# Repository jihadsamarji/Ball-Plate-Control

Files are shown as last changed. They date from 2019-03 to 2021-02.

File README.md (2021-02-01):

-------------------------------------
The Project is Still under Construction
-------------------------------------
# Ball-Plate-Control
This is a project done for a Master Thesis in the Electromechanical Engineering (specialization: Mechatronics),
it is about the design and control of a Ball and Plate Didactic Device.
This device is intended to be developed into a Commercial device and maybe sold to educational institutes or young apprentices in the field of Control Systems. 

The Project is Explained entirely on : [Presentation Video](https://youtu.be/tS8yI4Vpe_U) 

## Getting Started

These instructions will get you a copy of the project up and running on your local machine for development and testing purposes. See deployment for notes on how to deploy the project on a live system.

### Prerequisites

things you need to install before running the code:
- Arduino IDE
- Python 3.7
- Python PiP
- Python IDE (Pycharm is recommended)

Run the following commands in your command terminal after installing "PIP"
```
pip install opencv-python==3.4.5.20
pip install Django
pip install Pillow
pip install image
pip install imutils
pip install numpy
pip install pyserial
pip install pytz
pip install setuptools
pip install sqlparse
pip install wheel
```

## Deployment

- Make sure you run the "solveequation.py" code first to generate the dictionary file. (found in /Software/Lookuptable/)
- Then place the dictionary file called "data.txt" in the same directory of the "interface.py" code. (found in /Software/Interface/)
- Connect an Arduino and upload the arduino code "Full_Program.ino" using the arduino IDE.
- Make sure you have a Camera attached on your system. (otherwise, you will get an opencv error when running)
- Run the code "interface.py" . (found in /Software/Interface/) 

## Simulation Files
The simulation files are found in ( /Software/Matlab & Simulation/)

## Contributing

Please Contact me on jmz_mmz@hotmail.com for any contribution requests.

## Versioning

Versioning was done using GIT

## Authors

* **Jihad Alsamarji** - *Masters in Electromechanical Engineering* - [JISA_leb](https://github.com/jihadsamarji)

See also the list of [contributors](https://github.com/jihadsamarji/Ball-Plate-Control/graphs/contributors) who participated in this project.

## License

This project is licensed under the MIT License - see the [LICENSE.md](LICENSE.md) file for details

## Acknowledgments

I would first like to thank my thesis advisors and supervisors of the SAAS department at Université Libre de Bruxelles; Micheal KINNAERT, Laurent CATOIRE,Christoph MERTENS.
The door to my supervisors was always open whenever I ran into problems or had a question about my research or writing.
They consistently allowed this paper to be my own work, but steered me in the right direction whenever I needed it.
I would also like to thank the members of my dissertation committee - not only for their time and extreme patience, but for their intellectual contributions to my development as an Engineer.
In Addition, I like to express my gratitude to the open source Community that helped a lot in overcoming software and computational challenges during the study.
I must express my very profound gratitude to my parents, friends and to my girlfriend for providing me with unfailing support and continuous encouragement throughout my study and through the process of researching and writing this thesis.
This accomplishment would not have been possible without them.
Thank you.

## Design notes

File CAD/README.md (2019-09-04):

# Computer Aided Design
Please Proceed to the "/Thesis/test Bench/" folder to find the CAD files used to build the prototype.
The Asset folder, contains some 3d models found on the internet.

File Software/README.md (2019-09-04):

## Software Content
The software section is divided into several folder:
- Arduino (Contains equipment testing and calibration files and the final Full Program that is going to be running on the arduino in parallel with the image processing thread on the computer)
- Interface (Contains the GUI source code)
- LookUptable (Contains the code that generates a lookup table text file that helps the GUI to map between angle Alpha and Beta) 
- Matlab & Simulation (Contains the State space modelling and simulation files + simscape numerical simulation + recorded experimental data)

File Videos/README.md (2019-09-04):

# Ball-Plate-Control
## Videos
The submitted videos gives a demo of the GUI when the project was undergoing testing.

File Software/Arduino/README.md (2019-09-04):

#Arduino Files
To run the plant with the GUI you will be only needing the "Full_Program.ino" files.
The rest of the codes are only to test partially some functionalities of the equipments used for the plant.
You can notice that there is a file for the touchscreen, however, this was discontinued due to the extreme sensor noise.

## Caution 
All of these files are calibrated for a certain sensor and actuator that the Author owns. 
You should modify the calibration part of the code when using your own hardware.

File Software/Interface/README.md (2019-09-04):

# Interface (GUI)
The "interface.py" file is the code that contains entirely the GUI code, However, you should make sure that the lookup table which is the text file called "data.txt" is present within this directory to ensure that the code runs.
Another thing you should check is that a functional camera is attached to your system otherwise you will get opencv errors.
Lastly, you have the option to plot and record readings in realtime while using the GUI which will be stored in the "log.txt" file. This log file can be used with matlab later on to compare graphs.

##Additional information
The "Gettime.py" is just a simple code to record time delays between the GUI and the Arduino. You might actually never use this code, so please ignore it if you find it useless.

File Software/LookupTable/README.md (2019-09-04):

# Lookup Table Generation
Due to the non linear relation between the angle Alpha and Theta, a lookup table can be generated to map between these to angles by running the "solveEquation.py".
The generated file "data.txt" needs to be placed in the interface directory afterwards if you intend it to be used by the GUI.

## Caution
The "solveEquation.py" is manually adjusted to cope with the non linearities of the Author's actuator. So make sure you read it and understand it well, and then modify it to work with your actuator.

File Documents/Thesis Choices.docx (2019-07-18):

# Models (2 choices):

## 2 perpendicular Motors (with a base pole in the center):

Simpler (one motor to control orientation X and one for Y) (+)

Requires less Equipment -> Cheaper (+)

## 3 Motors 360/3 (without a base pole in the center):

More complex (any combination of 3 angles will give a certain inclination) (-)

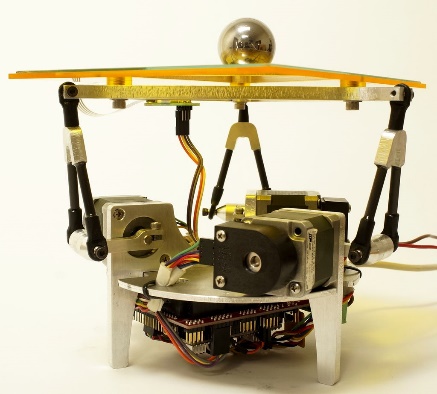
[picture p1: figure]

More Equipment -> More expensive (-)

Robust (+)

More of a Challenge (harder modelling and Control) (-)

# Requirements:

## Motors:

- Servo:

Easier to control (+)

Already comes with an encoder (+)

Much better for dynamic behavior (++)

Constant Torque to speed change (+)

Less power consumption (+)

- Stepper:

Harder to control (needs a drive) (-)

Needs an encoder for feedback (-)

Very accurate (++)

Higher power consumption (-)

## Position Sensor:

- Camera:

Requires a backend for image processing (--)

Can detect ball even if not on plate (predictive behavior) (++)

Adaptable for any kind of base shape (+)

Needs an Aditional Structure to hold the Camera (-)

- Resistive Touch screen:

Can only detect ball if ball Is on the base (no predictive behavior) (-)

Easy measurements (position X and Y) (++)

Limited to Base shape and Dimension (-)

No need for backend (++)

Noisy (---)

Requires a certain pressure to give readings (---)

## Control PCB:

- Arduino or Any Commercial Board:

Needs a Servo Shield module to power up the servos (-)

Commercially Available and Cheap (++)

Easy to Program and implement (+)

- Custom Made Board:

Needs time to Design and Build (--)

Needs Experience in Electronics and PCB design software (-)

Complicated and Hard to Program (-)

Customized for our Need → efficient and optimal (+)

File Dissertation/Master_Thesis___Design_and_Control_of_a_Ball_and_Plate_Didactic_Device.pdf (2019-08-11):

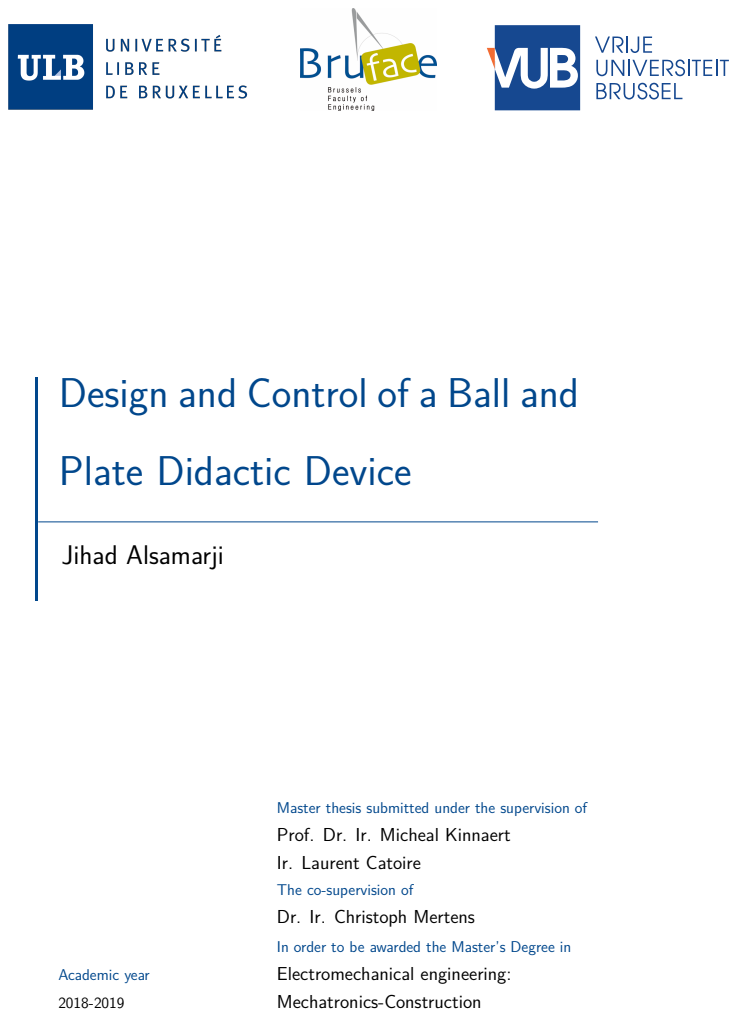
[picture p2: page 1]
Jihad Alsamarji; Academic year

Design and Control of a Ball and

Plate Didactic Device

Master thesis submitted under the supervision of
Prof. Dr. Ir. Micheal Kinnaert
Ir. Laurent Catoire

The co-supervision of
Dr. Ir. Christoph Mertens

In order to be awarded the Master’s Degree in
Electromechanical engineering:
Mechatronics-Construction

Abstract

This project tackles the design and control problem of a two DOF

ball and plate system to build a commercial didactic device that helps

young engineers to practice their control theory knowledge. Two sensing

techniques are proposed to measure the displacement of the ball; a resis-

tive touch screen or a camera with some image processing. The plant is

designed with CAD and operated using an arduino. A computer is also

connected to the plant for image processing using a GUI developed with

python. The plant is modelled and simulated using Matlab and Simulink.

Multiple PD controllers are compared and validated on the real system.

Keywords: 2DOF Ball and Plate System, Didactic Device, Mechanical Design,

Image Processing GUI, Control Design.

## Acknowledgement

I would first like to thank my thesis advisors and supervisors of the SAAS depart-

ment at Université Libre de Bruxelles; Micheal KINNAERT, Laurent CATOIRE,

Christoph MERTENS.

The door to my supervisors was always open whenever I ran into problems or had

a question about my research or writing. They consistently allowed this paper to

be my own work, but steered me in the right direction whenever I needed it.

I would also like to thank the members of my dissertation committee - not only

for their time and extreme patience, but for their intellectual contributions to my

development as an Engineer.

In Addition, I like to express my gratitude to the open source Community that

helped a lot in overcoming software and computational challenges during the

study.

I must express my very profound gratitude to my parents, friends and to my

girlfriend for providing me with unfailing support and continuous encouragement

throughout my study and through the process of researching and writing this

thesis. This accomplishment would not have been possible without them.

Thank you.

## List of Figures

1 | A demonstration of different Ball-Plate plants. From left to right:
2DOF, 3DOF and 6DOF | | 3
2 | A sketch of the 2DOF Ball-Plate prototype done prior to the
design stage | | 5
3 | Mechanical design dimensions (mm) | 11
4 | Mechanical design features | 12
5 | Electrical wiring of the touch screen sensor | 13
6 | Touch screen inner circuit taken from [7] | 14
7 | Pin states for reading each coordinate | 15
8 | Electrical wiring of the camera sensor | 15
9 | simple flowchart of touch screen code on arduino | 17
10 | Two programs running in parallel | 18
11 | Graphical user interface developped with the "Tkinter" library . . 19
12 | Live footage while tracking the ball, the reference point is also
shown as a small blue dot | 20
13 | A calibrated dictionary to map between the angle α and θ . . . . 21
14 | system dynamics | 22
15 | structural constraints sketch | 25
16 | Motion animation of the model using Simscape | 26
17 | Simscape Block diagrams of the model in Simulink | 26
18 | Comparison between the analyitical solution and the vertical rod
assumption | 27
19 | A Comparision of a response to a step input of 15 degrees. . . . 29
20 | A Comparision of a response to a step input of 17 degrees. . . . 30
21 | Impulse response | 32
22 | System Identification using impulse response | 32

Design and Control of a Ball and Plate Didactic Device | MA2-MECA
23 | System identification using step response (a step of 80 degree is
| used here to reach the maximum actuator angle) | 33
24 | Unitary Step response of the three identifications | 34
25 | System identified by avoiding the static friction | 35
26 | Simple closed feedback loop | 41
27 | Corresponding root locus with no controller | 41
28 | PD controller to fulfill the requirements | 43
29 | Step response of the plant by the aggressive PD controller. . . . 43
30 | Bode plot using the obtained PD controller | 44
31 | continuous time simulink model | 45
32 | discrete time simulink model | 45
33 | Reference tracking using the obtained PD controller on the final
| discrete non linear system | 46
34 | Controller command saturated at 0.26rad (14.9 deg) | 47
35 | Reference tracking using the perfectly tuned PD controller with
| the Parameters(P = 0.03, D = 0.02, N = 20) | 47
36 | Multiple ways to implement the low pass filter on the derivative
| action | 48
37 | Performance on the real plant(P = 0.03, D = 0.02, N = 20) . . . 49
38 | Comparison of performance for multiple PD controllers on the
| real plant | 50
39 | Tracking of a sinusoidal reference | 51

## List of Tables

1 | TGY-4409MD specs | 12
2 | Theoretical system parameters | 31

4

Design and Control of a Ball and Plate Didactic Device | MA2-MECA
3 | Ball configurations | 31

## Contents

1 Introduction | 1
1.1 Plant Requirements | | 1
1.2 Plant Selection | | 3
1.3 Plant Description | | 5
2 Design | | 6
2.1 Hardware Selection | | 6
2.1.1 | Actuators | | 6
2.1.2 | Sensors | | 8
2.1.3 | Processing Unit | | 9
2.2 Mechanical Design | 10
2.2.1 Reasoning | 10
2.3 Electrical Design | 13
2.3.1 | Resistive Touch Screen | 13
2.3.2 | Camera | 15
2.4 Software | 16
2.4.1 | Software for the Touch Screen | 16
2.4.2 | Software for the Camera | 17
3 Simulation and Control | 21
3.1 System Dynamics Modelling | 22
3.2 System Parameter Identification | 30
3.3 Control System Design | 35
3.3.1 States of Equilibrium: | 35

5

4 Results and Validation | 48
5 Discussion and Conclusion | 51
References | 53

Design and Control of a Ball and Plate Didactic Device | MA2-MECA

## 1 Introduction

Control system design is one of the toughest courses taught for young engineers

where one combines abstract mathematical knowledge and analysis with practical

engineering be it in mechanical, electrical, biomedical or other applications. An

Engineering student often finds his ways into solving dynamic equations ( differ-

ential equations) without a deep understanding of these equations and how they

are coupled together. A great idea to understand control theory is by working on

a physical plant and observe how do these equations manifest in the real world.

However, this idea of learning by working on a real plant is often not feasible

since it requires that the plant is affordable, available for the student to use,

portable so that the student can carry it home to experiment on and safe. So

the idea behind this thesis is to design and control a small physical plant that

will act as a didactic device for students in pursuit of learning control theory.

### 1.1 Plant Requirements

The requirements of such a plant are listed as follows:

- Portable : The ability to easily deploy or pack the plant, which means

that the plant needs to be lightweight, non fragile, easily assembled and

disassembled.

- Safe : The ability to be operated without any risk of harm nor damaging

the equipment by choosing extreme control parameters.

- Affordable : The plant should be affordable for students and therefore the

hardware selection and manufacturing should be optimal for its usage.

- Controllable : The plant should be designed in a way that allows an external

1

Design and Control of a Ball and Plate Didactic Device | MA2-MECA

input to move the internal states of the system from any initial state

to any other final state in a finite time interval. This is valid when the

controllability matrix R = [ B AB A²B ... An−1B] is full rank (rank(R) =

n) where n is the number of the states. Theoretically, With such an ability,

one can arbitrary alter the system’s eigenvalues¹ by an input u = −Kx

which gives x˙ = (A − BK)x , where the control gain matrix K can be

chosen arbitrarily for pole placement. A controllable system in continuous

time is equivalent to a system with a full reachability thus with a reachable

set Γ = IRn
. However, in practice, the actuators should have a sufficient

actuating range to ensure controllability. [ example : if one linearizes the

system of an automobile and find out that it is controllable, it doesn’t mean

that the automobile can reach a far destination with a blink of eye by using

a controller with an enormous gain, because in reality, the actuators are

saturated with certain limits and hence a non linear system.]

- Robust: The plant should be stabilizable with a reasonable gain and phase

margin, meaning that with any small change to the transfer function of the

system, it can still achieve stability by the same controller. In other words,

using the Nyquist stability criterion, the further away our system’s Nyquist

plot is from the point (-1,0.j) the more it is robust to model uncertainty,

delays, higher control gains, noise and disturbance.

- Scalable : the plant could be targeted to an educational institute as well

where the required size of the plant is to be bigger. Therefore, the plant

should be able to be scaled mechanically and electrically with no major

changes to the plant’s dynamics and therefore to its control schemes. Fur-

1
there is a link between the eigenvalues of state matrix A and the poles of the corresponding

transfer function. All the poles are eigenvalues of A, but the vice versa is not true since

cancellations with the numerator can happen. [1]

2

Design and Control of a Ball and Plate Didactic Device | MA2-MECA

thermore, the plant should support a wide range of controllers from classical

to advanced, modern and optimal control based on user experience.

- Convenient : The main purpose of the plant is to be didactic and targeted

for young engineers, therefore, it should be simple and self explanatory with

no abstractions. Usually mechanical systems tend to have less abstractions

since you directly feel and see the change of any control parameter and

you witness the manifestation of the governing equations in real life.

### 1.2 Plant Selection

Now that the plant’s constraints are determined, several choices can be made.

In fact, the Ball and Plate is a perfect candidate since it’s unstable by default

and tricky to control. This plant gives space to apply many control methods and

results in different behaviors which are interesting to be analyzed and compared.

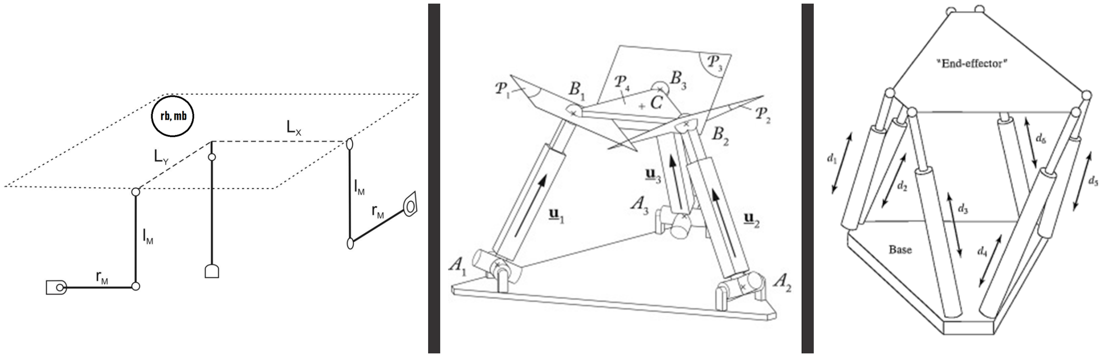
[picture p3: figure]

Figure 1: A demonstration of different Ball-Plate plants. From left to right:

2DOF, 3DOF and 6DOF

There exist many forms of the Ball-Plate plant which differ by the number of

degrees of freedom ( Some of these Plants are shown in fig.1). The objective is

3

Design and Control of a Ball and Plate Didactic Device | MA2-MECA

always to control the position of the ball at least in the X and Y directions. The

system is MIMO²
since it requires two states to be measured and two actuators

to be controlled.

In a 3 DOF Ball-Plate, at least 3 actuators are needed. Each combination of

these 3 driving angles will result in an inclination around the X and Y axis and

a displacement in the Z direction which is often ignored. Since the resulting

inclination is a function of all actuator angles, the outputs are coupled and this

can be seen in the system’s governing equations.[6]

Remark: In 2DOF Ball-Plate, each actuator is responsible for one degree of free-

dom since the ball motion in the X and Y directions are decoupled. Therefore,

decentralized control can be used by treating this MIMO system as two sepa-

rated SISO systems where each direction is actuated, measured and controlled

separately. (more on that later)

For the sake of simplicity and affordability, the 2 DOF plant is chosen for this

study.

2Multiple-input and multiple-output

4

Design and Control of a Ball and Plate Didactic Device | MA2-MECA

Figure 2: A sketch of the 2DOF Ball-Plate prototype done prior to the design

stage.

### 1.3 Plant Description

Ball-Plate is a system that holds balance of a ball on a plate or board. The

actuators allow the plate to be oriented with a certain angle of inclination to

counterbalance the motion of the ball. A sensing device should be able to extract

the position of the ball in the two axes and feed it to the controller which will

determines the position, speed and acceleration of the ball and therefor process

the right command for the actuators. The controller will also counter act the

destabilization of the ball by any disturbance be it an external force or noise in

the system. A first sketch of the prototype is drawn in fig.2.

5

Design and Control of a Ball and Plate Didactic Device | MA2-MECA

## 2 Design

### 2.1 Hardware Selection

Before proceeding to the mechanical design, one should plan ahead on which

hardware is suitable for such a device and then design accordingly.

### 2.1.1 Actuators

Knowing that our plant is 2 DOF, the Plate is going to be tilting around it’s

pivoting point in the center. There are two actuators to be placed perpendicularly

to tilt the plate around the two axes ( X and Y). Based on their distance from the

center, the ratio between the angle of the plate and the angle of the actuators

can be determined. However, to fully utilize the actuators, only a range of 180

degrees is needed. To achieve zero steady state error, it is crucial that the

actuators are accurate. Any error in the angle of the actuator will lead to an

error in the angle of the plate. The ball is sensitive to roll over uneven surfaces,

meaning that with an inaccurate actuator, a steady state is hard to be achieved.

The two most suitable actuators for such a plant are the Servo motor and the

stepper motor.

- Stepper motor : often comes without an encoder nor a drive and therefore

they are needed to be bought separately, installed and controlled. Steppers

exist in 4,6 or 8 wire configurations. All of the stepper wires are to power

the different coil pairs. Different powering of the coils will result in different

rotation direction and step accuracy. The frequency of powering these coils

determines the step speed. Manually managing the powering of the coils

is troublesome and requires complex circuitry, that is why a stepper drive

6

Design and Control of a Ball and Plate Didactic Device | MA2-MECA

is necessary for such purpose. Even a stepper motor can miss some steps

and that is why an encoder is used to feedback and eliminate error. The

torque-speed curve of the stepper motor shows that the torque decreases

with an increase of speed. To add things up, steppers consume current

continuously even when idle unless it is controlled not to do so.

- Servo motor: is nothing but a DC motor attached to a gear box for speed

reduction and higher torque. It comes packed with an internal circuitry

that contains an encoder and a controller. It is only powered by two

cables and commanded via a third cable in the form of PWM (pulse width

modulation). Servos have almost a flat relationship between torque and

speed. Servos only consume current when needed which enables them to

run much cooler.

To summarize, Servo control systems are best suited to high speed, high torque

applications that involve dynamic load changes. Stepper control systems are less

expensive and are optimal for applications that require low-to-medium accelera-

tion, high holding torque and the flexibility of open or closed loop operation.[4]

For the Ball-Plate, high speed actuation is needed to cope with the reference

tracking or else there will be delays in the system which makes the plant uncon-

trollable in practice. Since the actuators are going to be varying their rotating

speed continuously, a flat torque-speed behavior is needed. Using Steppers will

complicate the circuitry, take much more space, consume more power and cost

more in case of closed loop operations. With that being said, servo motors are

chosen as actuators for this study.

Due to the need of a High speed and moderate torque, a standard sized Servo

motor will be chosen in the next section after revealing some additional mechan-

ical constraints.

7

Design and Control of a Ball and Plate Didactic Device | MA2-MECA

### 2.1.2 Sensors

Only one displacement sensor is needed for a full state estimation (proven in

the observability study done in section 3.3). A reliable sensor measurement is

of utmost importance since any noise, inaccuracy or processing time delay, will

induce instability. Two ways to detect the displacement of the ball are proposed.

- Camera : a camera can be placed on top of the plate to monitor the

upper side of the plate. Of course, a bare image will not carry any useful

information of the ball and therefore, the image should be processed either

by movement detection or by color filtering. Even though this will require

a back-end for image processing and hence delay, the readings will be

extremely accurate and noise free.

- Resistive touch screen : another way of measuring the displacement of

the ball is to place a resistive touch screen which is sensitive to the ball’s

touch pressure. This solution is definitely simpler since it doesn’t require

any processing. However, the touch screen has a certain touch pressure

threshold to start reading inputs. This threshold is something not to be

underestimated since the touch pressure of the ball will decrease when the

ball is moving or even worse if the plate is vibrating. Vibration causes

the ball to be lifted from the screen’s surface which makes it undetectable

anymore. On the other hand, the touch screen is going to have noisy

readings that need to be filtered since it cause additional vibrations specially

from the derivative gain in the controller.

Even with the difficulties of the resistive touch screen option, both of these

sensing methods will be used and compared later in the study.

8

Design and Control of a Ball and Plate Didactic Device | MA2-MECA

### 2.1.3 Processing Unit

Now that the actuators and sensors are known, a suitable processing unit can

be chosen to act as the controller. For the sake of simplicity and since this

study focuses only on the design of the prototype and not the final product, a

commercial controlling unit will be used instead of a custom built PCB. For this

purpose, the Arduino Uno is enough for the task.

The Arduino boards are mainly composed of a microcontroller around which

there are many input and output pins that allow the board to interact with

external electronics. Several models exist, the major difference that separates

them is the number of i/o pins. Another difference is in the memory size of the

microcontroller. For example a microcontroller contained in an Arduino Mega

will contain an EEPROM with a capacity of 4kB while an Arduino Uno will have

an EEPROM limited to 1 kB. These cards allow anyone to design a project at

a lower cost. An Arduino Uno costs around 20 euros which makes these cards

accessible. Another advantage is the huge open-source community, where people

post tutorials and help with projects on the internet. Furthermore, Arduino also

provides free programming software that allows to easily program any Arduino

or other cards with a similar microcontroller. Indeed the Arduino software can

also be used to program a custom made card with the same bootloader. This is

an example of one of the many benefits that open-source software offer.

Knowing that the arduino is not suitable for image processing, a computer will

be attached to the plant only in case of using the camera. However, the Arduino

is always going to be used to send PWM signals to the servos.

9

Design and Control of a Ball and Plate Didactic Device | MA2-MECA

### 2.2 Mechanical Design

There is no perfect design. Designing is an iterative procedure to reach a better

product, It begins by fixing assumptions and determining the unknowns. Based

on the availability in the market, ease of manufacturing, cost and efficiency, the

following assumptions are taken :

- Size of the actuated plate (30x30cm is a reasonable space to experiment

different ball movement patterns and tolerate a bit of overshoot)

- Height of the actuated plate (27cm is comfortable to reach and doesn’t

require a tall camera pole).

- Size of the supporting bench (50x30cm is enough to contain all of the

plant).

- Size of the servo frame (Standard size is used to match the selected servo

motor in the previous section) .

- Material and thickness of the plate and bench (4mm Ply-Wood is used

since it is available and easy to be cut).

- Carbon fibre is used for the actuating rods and the supporting structure of

the camera.

- PLA is to be used for 3d printing of additional supporting structure.

### 2.2.1 Reasoning

- The joints between the servo arms and rods need to convert the rotation

motion into a linear motion while keeping the rods free to rotate. This

can be achieved by a rod end bearing joint or even better handled with the

10

Design and Control of a Ball and Plate Didactic Device | MA2-MECA

rocker ball joint to compensate for any misalignment during motion.

- Another special joint needs to be placed between the rods and the plate to

allow the latter to be pivoting around 2 axis while connected in 3 places.

This can be done by a universal joint or a magnetic ball joint.

- The distance dc and dm shown in fig.14 are very important since the ratio

κ =

dc
dm

defines the relationship between the angle θ of the servos and the

angle α. The bigger κ is, the bigger the range of θ is needed

- To leave some flexibility in the assembly phase, some slide tracks are cut in

the bench that allow for adjustments by sliding of the camera pole, servo

supports and central plate pole.

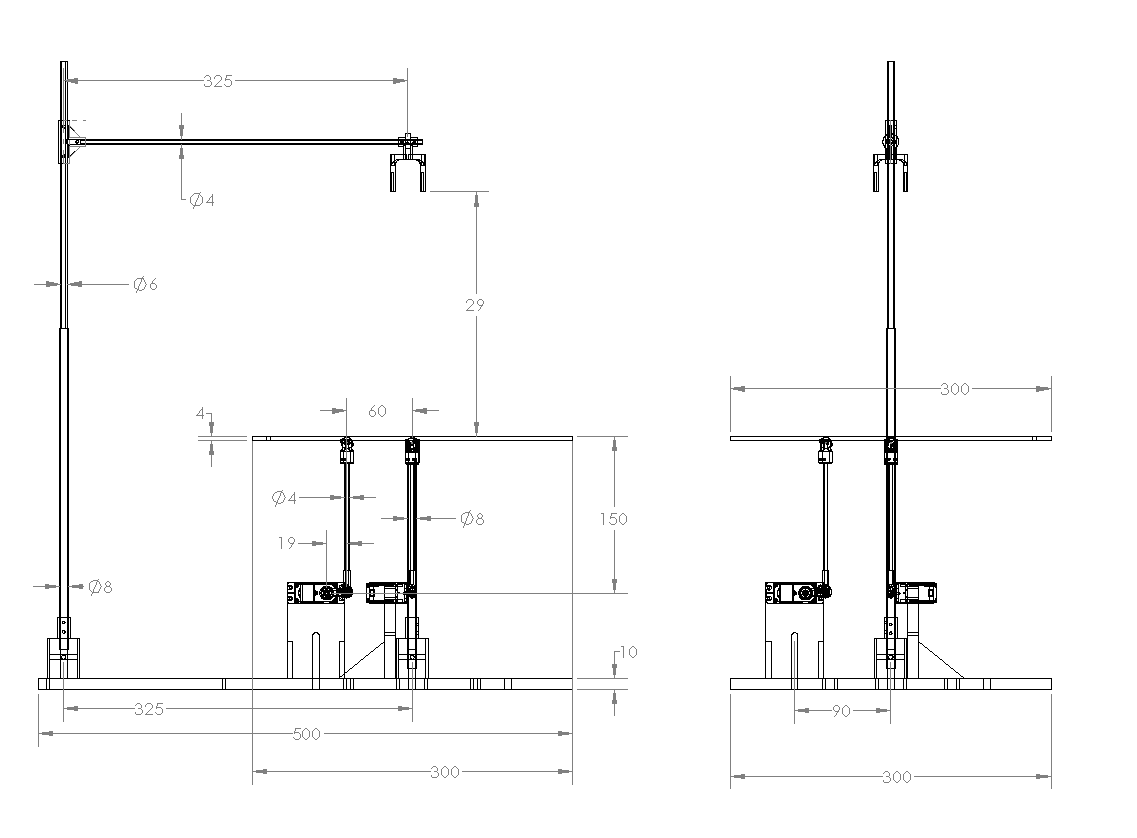
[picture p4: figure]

Figure 3: Mechanical design dimensions (mm)

11

Design and Control of a Ball and Plate Didactic Device | MA2-MECA

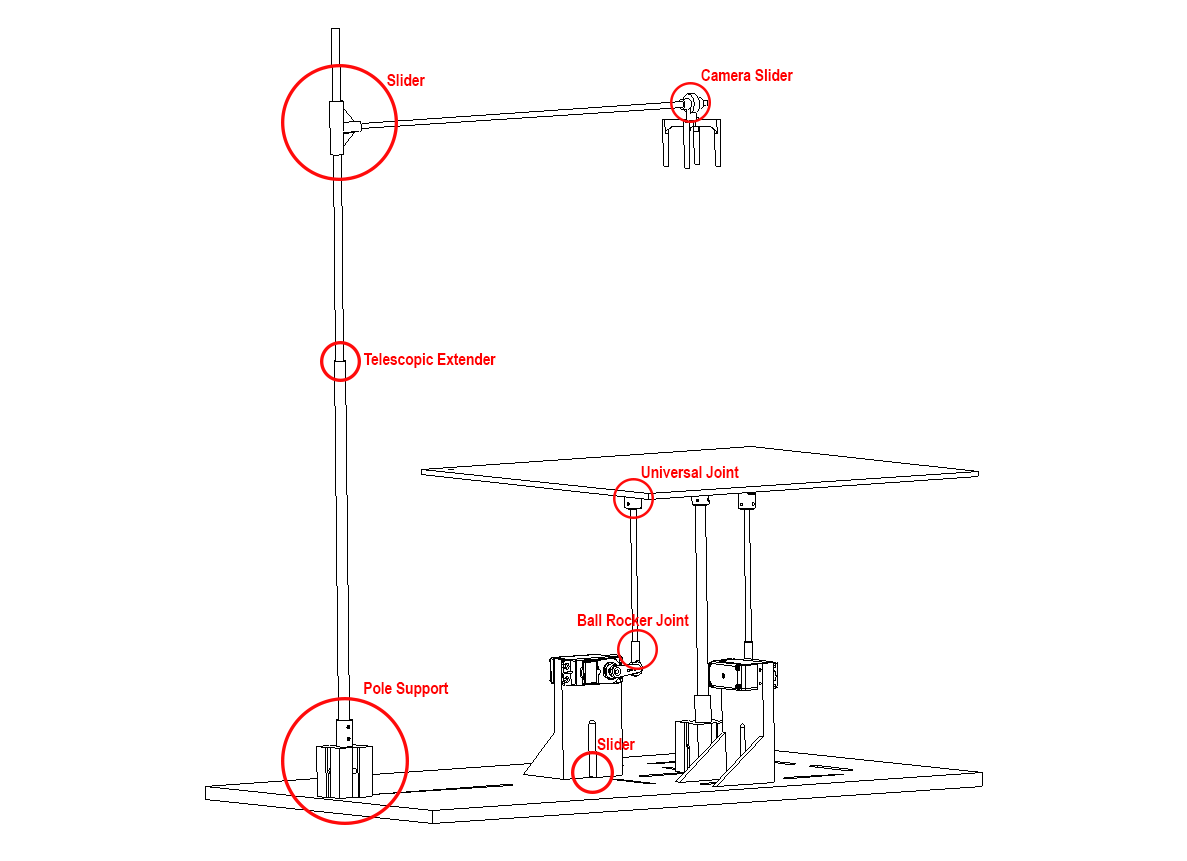
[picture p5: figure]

Figure 4: Mechanical design features

Now that the mechanical design is more detailed, the plate is going to be sup-

ported in 3 places. The plate is going to be made out of ply wood. Assuming

an iron solid ball of 0.1 kg to be rolling on the surface. Assuming a critical

situation where the total weight is handled by one servo arm. Roughly speaking,

a torque of 8N.cm is needed. The "TurnigyTM TGY-4409MD" was chosen as

the actuator since it packs the torque needed, fast enough and relatively cheap.

TGY-4409MD | 4.8 V | 6.0 V
Speed (in second / 60◦ ) | 0.13 | 0.11
Torque (in Kg.cm) | 8.65kg.cm | 9.45kg.cm

Table 1: TGY-4409MD specs

Remark: As a matter of fact, servo motors shouldn’t be chosen only by their

12

Design and Control of a Ball and Plate Didactic Device | MA2-MECA

rated specifications. For this kind of application, their control circuitry is of

much importance since a high speed high torque servo is useless if it takes time

to respond. Not just response time but also the accuracy plays a big role in

stabilizing such a plant.

### 2.3 Electrical Design

The circuits used for each of the sensing methods are rather simple as discussed

in the hardware selection section.

### 2.3.1 Resistive Touch Screen

Figure 5: Electrical wiring of the touch screen sensor

As shown in fig.5, the arduino is fed from the same power source of the servos(

given that the power source can supply the maximum current drawn from all of

the component). The touch screen used in this project contains 4 wires (X1 X2

Y1 Y2), X1 and X2 are connected inside the touch screen and the same goes

13

Design and Control of a Ball and Plate Didactic Device | MA2-MECA

for Y1 and Y2. The connectivity inside the screen is a resistive one as shown in

fig.6.

Figure 6: Touch screen inner circuit taken from [7]

The 2 connections are shorted whenever pressure is applied, this will create a

voltage divider. The horizontal and vertical coordinates of a touch can be read

in two steps. First, Y1 is driven high, Y2 is driven to ground, and the voltage at

X1 is measured. The ratio of this measured voltage to the drive voltage applied

is equal to the ratio of the vertical coordinate to the height of the touch screen.

Horizontal coordinate can be similarly obtained in the opposite manner. Both

measurements can be shown in fig.7.

14

Design and Control of a Ball and Plate Didactic Device | MA2-MECA

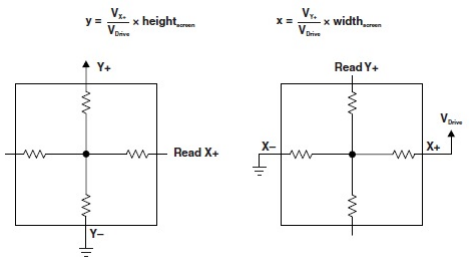
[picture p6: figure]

Figure 7: Pin states for reading each coordinate.

Therefore both measurements cannot be taken in the same time. The Arduino

will flip the pins whenever a reading command is signaled. Lastly, the resistors

hooked in fig.5 are pull-down resistors to pull the voltage down to ground if there

was no touch.

### 2.3.2 Camera

The circuit used with the image processing is shown in fig.8.

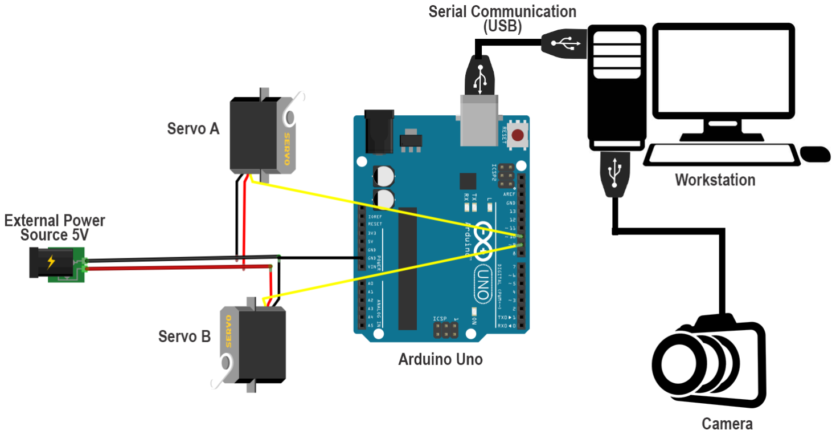
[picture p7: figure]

Figure 8: Electrical wiring of the camera sensor

15

Design and Control of a Ball and Plate Didactic Device | MA2-MECA

In this setup, the serial connection between the Arduino and the computer is to

receive command signals and power the Arduino in the same time. The camera

is a digital sensor that sends a picture every sampling time ts = 0.033s. The

picture is then processed to find the position of the ball in pixels. Based on the

chosen control law, the computer will give a command signal in the form of an

angle θ for each servo. The arduino will translate the angle into a PWM³ signal

for each of these servos.

### 2.4 Software

In this section, a brief methadology of the software design is going to be explained.

However, The full software implementation is shown in the appendix.

### 2.4.1 Software for the Touch Screen

By using the touch screen, a simple C code can do the job by applying the

following algorithm:

3Pulse width modulation

16

Design and Control of a Ball and Plate Didactic Device | MA2-MECA

Figure 9: simple flowchart of touch screen code on arduino

The latter flowchart doesn’t specify any kind of control law, the last block in

the code is used to save some states such as the (error) in case of using an

integrator. The only complication that could arise with using the touch screen is

the filtering of the noise. Having a bad quality touchscreen or having a ball that

weights so close from the threshold pressure can result in noisy measurements.

Therefore, many filtering techniques can be applied such as the average, median

, low pass, high pass, notch, band pass filter... Filtering doesn’t come cheap, by

requiring more measurements, that will produce delay and require more memory.

### 2.4.2 Software for the Camera

Even though using the camera would requires a higher processing power than an

arduino such as a computer, this approach is much encouraged and appreciated

17

Design and Control of a Ball and Plate Didactic Device | MA2-MECA

knowing that it will be almost noise free. The following algorithm was used:

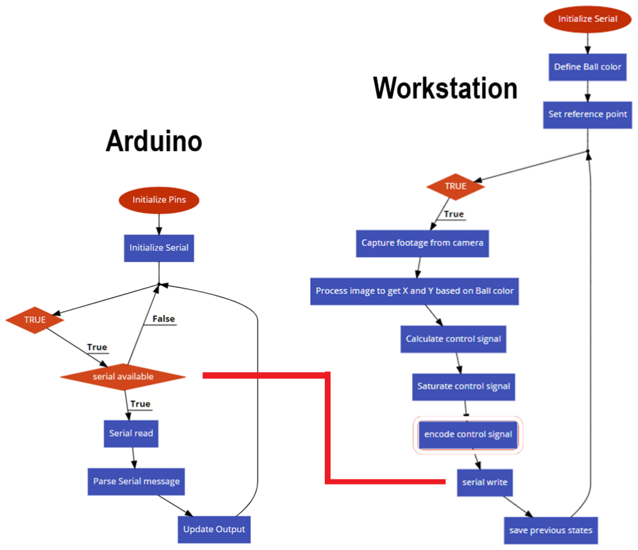
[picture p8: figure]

Figure 10: Two programs running in parallel

As shown in the latter algorithm, the code running on the workstation commu-

nicates with the Arduino by a serial COM, therefore, the speed at which the

arduino respond is defined by the baud-rate.

The Image processing was done using the OpenCV library which contains many

useful features such as Image editing and filtering based on color or motion.

Furthermore, a python3 GUI was designed to be executed on the workstation to

allow the user to manipulate some parameters in real time as shown in fig.11.

18

Design and Control of a Ball and Plate Didactic Device | MA2-MECA

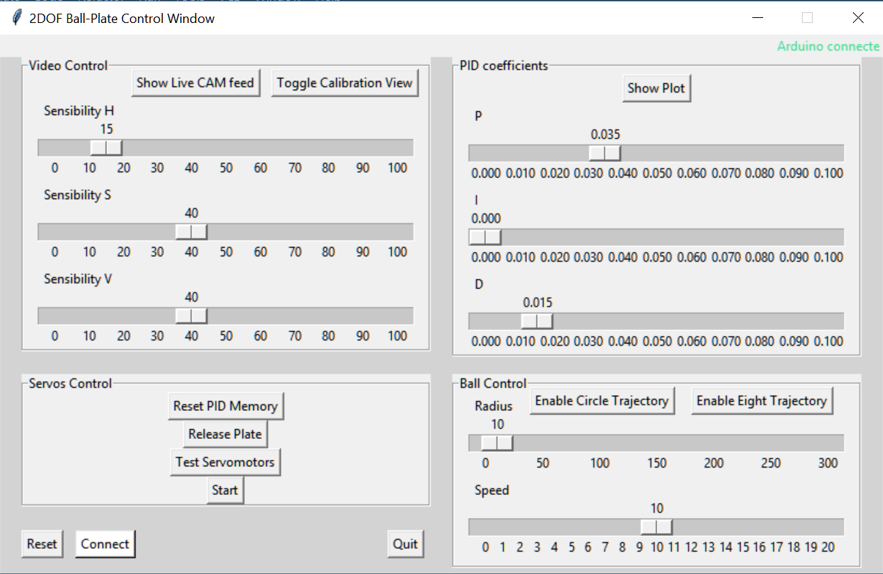
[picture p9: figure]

Figure 11: Graphical user interface developped with the "Tkinter" library

The GUI also allows the user to give Patterns to track such as circular trajectories.

The user can monitor in realtime the reference tracking inside the GUI graph

plotter. Also, the GUI displays the footage of the camera in realtime and allows

the user to change the reference point or the ball color to be tracked on screen

using the mouse buttons (as shown in fig.12.

19

Design and Control of a Ball and Plate Didactic Device | MA2-MECA

Figure 12: Live footage while tracking the ball, the reference point is also shown

as a small blue dot

Indeed the development of the GUI was a whole project by itself, but it was a

mandatory tool to interact with the plant in an easy and fast way. Finally, Instead

of solving for the angle analytically in each cycle, the non linear relationship

between the servo angle and the angle of the plate is done in a look-up table

(called Dictionary in python) as shown in fig.13.

20

Design and Control of a Ball and Plate Didactic Device | MA2-MECA

Figure 13: A calibrated dictionary to map between the angle α and θ

## 3 Simulation and Control

Before doing any control on the real plant, the system should be modelled and

simulated on Matlab to fully understand the dynamics evolving around it to have

an idea of what to expect in reality and what control method should we use

to achieve our requirements. Modeling and simulation are important to solve

problems safely and efficiently, It allows us to analyze and easily validate the

theory with the real plant. Even though the Ball-Plate is safe to be operated

even with false parameters, as an engineer, one should always model the problem

at hand and avoid the trial and error approach. In other words, modelling could

save money and time, avoid risks, gives better visualization of the dynamics,

solves directly for the optimal result, handles uncertainty. For this purpose,

Matlab and simulink are going to be used.

21

Design and Control of a Ball and Plate Didactic Device | MA2-MECA

### 3.1 System Dynamics Modelling

For the sake of simplicity and since our problem can be decoupled by separating

the X from the Y direction, only one of these direction will be studied (fig.14

shows the model in the X direction).

Figure 14: system dynamics

The mathematical formulation will only be conducted on the X direction since

the Y direction is the same. Equation of motions can be obtained using the

classical approach by working on the free body diagram or by using the Hamil-

tonian, Virtual work or Langrangian formulation. For the sake of simplicity, the

Lagrangian formulation was used in this study:

d
dt

∂L
∂q˙i

−

∂L
∂qi
= Qi | (1)

Where L is the langrangian and Qi

is the external forces acting on the system

generalized coordinate qi

, in this case qi will be the x coordinate.

The lagrangian L can be written as :

L( ˙qi

, qi) = T( ˙qi

, qi) − V (qi) | (2)

22

Design and Control of a Ball and Plate Didactic Device | MA2-MECA

Where T is the system total kinectic energy and V the total potential energy.

Both of them are in function of the generalized coordinate qi which is x.

Now, we can seperate T into the linear component Tl and the rotational com-

ponent Tr Component:

Tl =

1
2

mbxḃ

2
(3)

Tr =

1
2

Iω²
b

(4)

Where mb is the mass of the ball, xb is the ball’s displacement, , I is the ball’s

moment of inertia and ωb is the angular velocity of the ball. Note that I depends

on the shape of the ball where I =

2
5mbr

2
b

in case of a solid sphere and I =

2
3mbr

2
b

in case of a hollow sphere.

by replacing ωb with xḃ
rb

, the resulting total kinetic energy will be :

T =

7
10

mbxḃ

2
(5)

Solid sphere

T =

5
6

mbxḃ

2
(6)

Hollow sphere

Now for the potential energy:

V = mbg.xbsin(α) | (7)

Where g is the gravitational acceleration and xb.sin(α) is the x component of

the gravitational force (weight).

23

Design and Control of a Ball and Plate Didactic Device | MA2-MECA

To get back into solving the Lagrangian equation (1), the only composite force

actuating on the qi

is the friction Fx which can be written as Qi = Fx = −fcxḃ

and hence:
7
5

x¨b +

fcxḃ
mb
+ g sin α = 0 | (8)

Equation of motion of the ball in case of Solid sphere

5
3

x¨b +

fcxḃ
mb
+ g sin α = 0 | (9)

Equation of motion of the ball in case of Hollow sphere

The obtained equation will be nonlinear (includes a trigonometric term). There-

fore, it will have to be linearized around the equilibrium⁴ point.

Bear in mind that the input of our system is not the angle α, it is the reference

angle of the servo θr. A generic second order relation is assumed for the servo-

motor dynamics in:

¨θ + 2ζωn

˙θ + ω
2
n

θ = ω

2
n
θr | (10)

Where ωn is the motor’s natural frequency ζ is motor’s damping ratio and ωr is

the reference servo angle.

Remark: assuming second order dynamics to the servo motor and assigning the

parameters ζ and ωn arbitrarily based on the rated specifications is a big step

toward system uncertainty. Therefore, system identification is a great method to

capture the real dynamics of the system. This will be done in the next section.

To connect the equation of the servo motor with the equation of motion of the

4An equilibrium point is a point such that, in the ideal case, maintaining constant the input,

the state “does not move”. Note that in real nonlinear systems, there may be several points

of equilibrium.[1]

24

Design and Control of a Ball and Plate Didactic Device | MA2-MECA

ball, there is a relation between the angle α and θ:

dm sin θ = dc sin α | (11)

where dm is the length of the servo arm and dc the distance between the center

of the plate and the linking arm. this can be reduce by using κ =

dc
dm

sin θ = κ sin α | (12)

Remark: the latter relation between α and θ is obtained assuming that the

linking rod is quasi vertical, meaning that the angle ψ in fig.15 is zero. This is

not the case in real life, therefore a position kinematic analysis will be done.

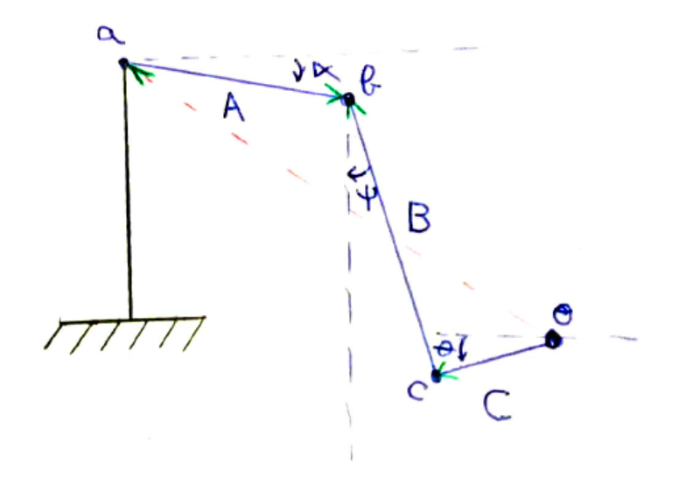
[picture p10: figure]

Figure 15: structural constraints sketch

Looking at fig.15, the structure is a 4 bar mechanism, so the constraint equation

is obtained from the requirement that the distance B between the moving pivots

a and b is constant throughout the movement of the linkage. The symbols A,B,C

are used as lengths in this section and they will be used later for other purposes

in the state space matrix. The constraint equations are :

~oc + ~cb = ~oa + ~ab | (13)

25

Design and Control of a Ball and Plate Didactic Device | MA2-MECA

projecting this equation on the horizontal and vertical planes gives:

−C.sin θ

−C. cos θ

- +

B. cos ψ

−B.sin ψ

- =

B

A + C

- +

A.sin α

A. cos α

- (14)

For a given angle θ, solving for α by hand can be troublesome. therefore, an

analytical solution is hard to reach. By using the Simscape library in Simulink, we

can build the geometrical structure and plot the numerical relationship between

α and θ.

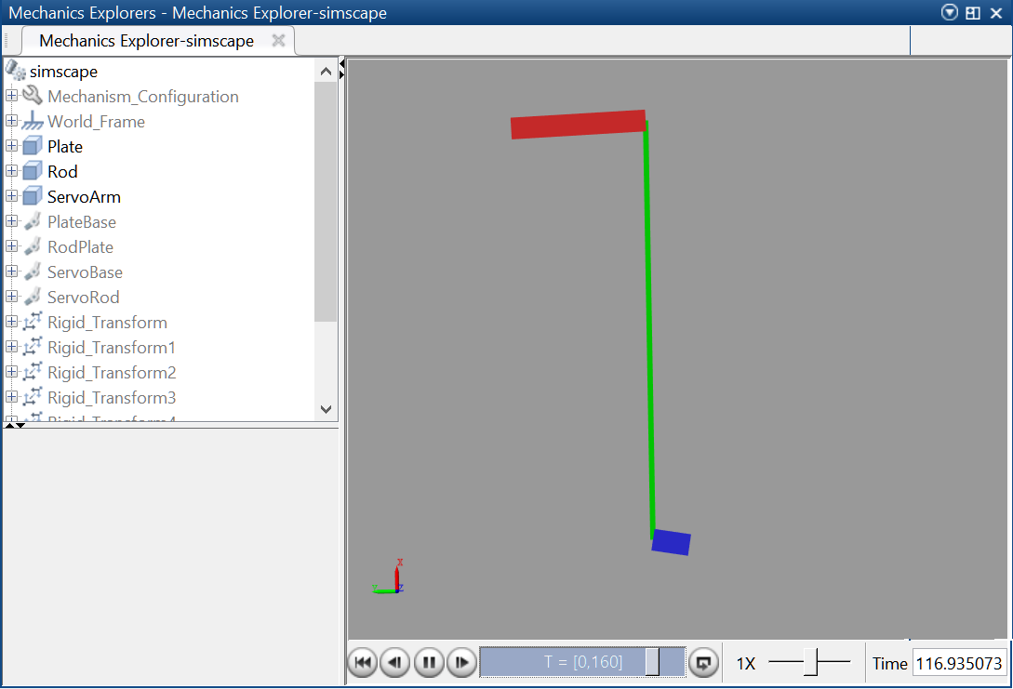
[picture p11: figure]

Figure 16: Motion animation of the model using Simscape

Figure 17: Simscape Block diagrams of the model in Simulink.

26

Design and Control of a Ball and Plate Didactic Device | MA2-MECA

After obtaining the analytical solution for the relation between α and θ, a com-

parison with the assumption in equation(11) is shown in fig.18

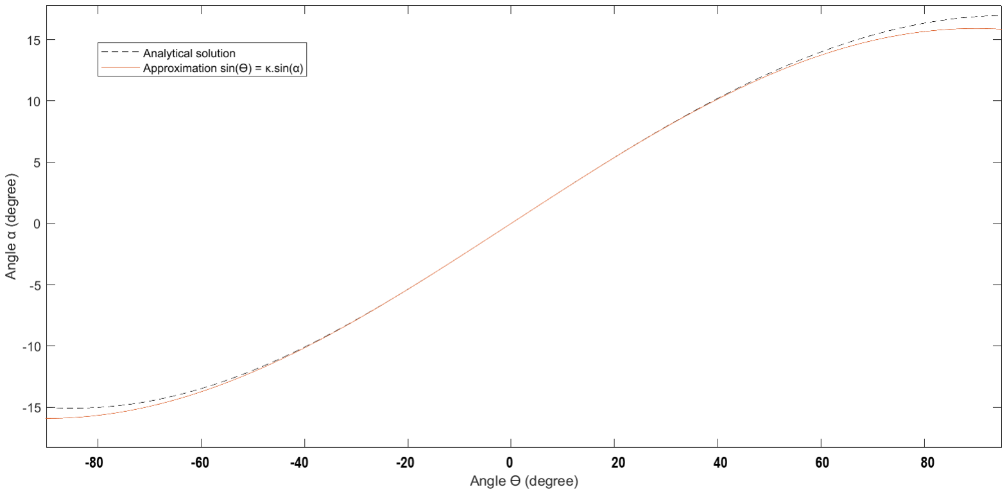
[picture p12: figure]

Figure 18: Comparison between the analyitical solution and the vertical rod

assumption

It can be said that the assumption is a very close approximation throughout the

operating region. Therefore, the relation dm sin θ = dc sin α will be adopted in

this study.

As discussed earlier, the trigonometric terms needs to be linearized around the

state of equilibrium in order to come up with a control design, however, we

can use a look up table to map the relation between α and θ upon using the

real plant. The angle α is designed to be contained between -15◦

and +15◦

which means that sin α can always be linearized around the point of equilibrium

0

- which further means that sin α ≈ α. The same linezarization goes for the

servo motor angle θ around 0◦ where sin θ ≈ θ, however this relation only holds

between -15◦

and +15◦
and other linearizations need to be done to cover the

27

Design and Control of a Ball and Plate Didactic Device | MA2-MECA

whole range of the servo’s operating angle for a more accurate modeling.

θ = κα | (15)

This will give us the equation that will be used to connect the system’s input αr

to the system’s output xb.

α¨ + 2ζωnα˙ + ω

2
nα = ω

2
nαr | (16)

Remark: notice that the plate’s equation of motion copied the servo motor

dynamics without adding any kind of friction due to the joints or vibrations due

to the stiffness of the rods. This is also an uncertainty that will be validated in

the next section.

Now that the fundamental equations and relations are all at hand, the state

space⁵ of the continuous linear time invariant⁶
system can be constructed using

the general representation :

q˙(t) = A.q(t) + B.u(t) | (17)
y(t) = C.q(t) + D.u(t) | (18)

where q = [ xb xḃ α α˙ ]

T
are the system’s states and u = αr is the system’s

input and y = xb is the output. the matrices A, B, C and D are shown in the

5Local input/state/output representation
6The system is time invariant to any temporal translation. (or equivalently the output

doesn’t depend explicitly on the time)

28

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

Design and Control of a Ball and Plate Didactic Device | MA2-MECA

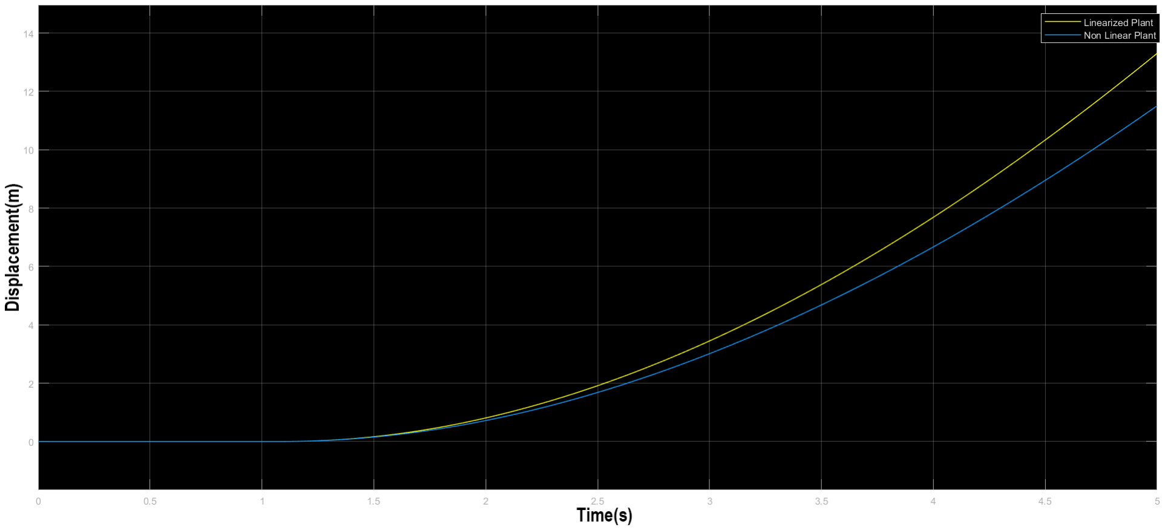
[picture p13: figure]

Figure 20: A Comparision of a response to a step input of 17 degrees.

Remark: The comparison done in both fig.19 and fig.20 shows that the obtained

LTI is a good approximation of the non linear system as long as the operating

range is ±15 degrees.

### 3.2 System Parameter Identification

Bear in mind that this section is only purposed to choose and validate the system’s

parameters and not to totally identify the system as a black box. It’s more like

a grey box approach where we already know the theoretical model of the system

and we’re interested to notice the differences with the real plant.

Without this section, the parameters that should have been used are shown in

table.2 and table.3.

The shown parameters, are all measured except for ωn and ζ were assumed based

on the servo’s rated specifications. Since the servos are going to be loaded and

attached to the plate, the assumed parameters cannot be trusted and therefore

needs validation.

30

Design and Control of a Ball and Plate Didactic Device | MA2-MECA
Symbol | Value
ωn | 19rad/s
ζ | 1
fc | 0.001Ns/m
g | 9.81m/s²
dm | 0.017m
dc | 0.062m

Table 2: Theoretical system parameters

Configuration | Description | rb (m) | mb (kg)
1 | Hollow steel | 0.016 | 0.013
2 | Solid Iron | 0.01 | 0.046
3 | Hollow Ping Pong | 0.02 | 0.001
4 | Solid Marble | 0.007 | 0.0049

Table 3: Ball configurations

Since the point of interest lies in validating the equation governing the dynamics

of the plate due to a reference angle αr as an input, a good idea is to apply

system identification to get the transfer function regarding equation (14). The

procedure requires a sensor to measure the angle α resulting from an input αr.

Measuring the angle α requires a potentiometer to be attached on the central

pivoting point of the plate. This measurement method is time consuming and

requires a clock module to be connected on the arduino to know the absolute

time of the measurement and sync it with the input. A simpler way is to place a

smart phone on top of the plate and connect it to MATLAB by wifi and capture

the readings of the phone’s gyroscope to get the angle α. To sync the input signal

with the measurements, the absolute time of both signals is known and can be

31

Design and Control of a Ball and Plate Didactic Device | MA2-MECA

matched using simple MATLAB matrix manipulations. A sampling frequency of

90Hz was used.

Figure 21: Impulse response

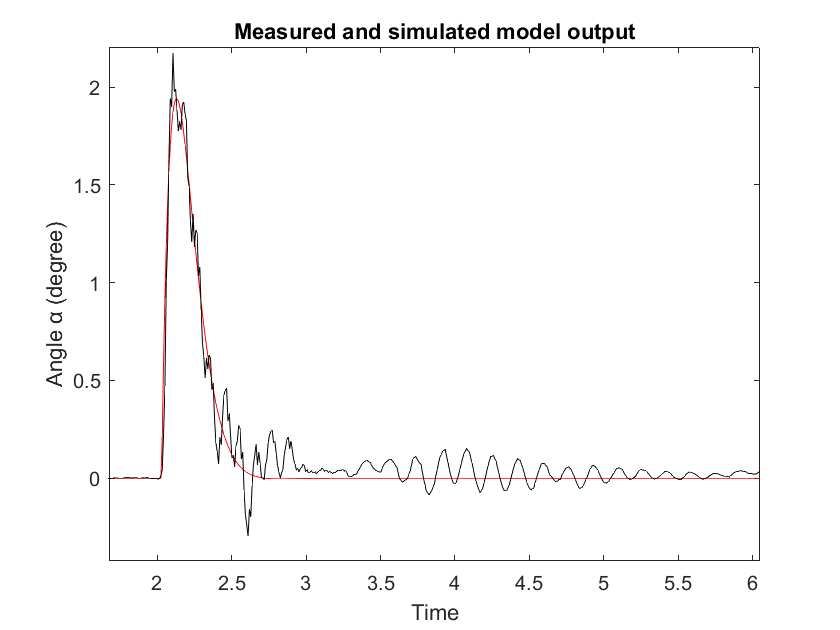
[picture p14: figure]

Figure 22: System Identification using impulse response.

As a first attempt, the impulse response was captured in fig.21 and then identified

as a second order system in fig.22.

32

Design and Control of a Ball and Plate Didactic Device | MA2-MECA

Remark: The latter observation gives us a possible way to identify the transfer

function of an unknown linear system in the case we are able to measure re-

liably the impulse response ! It must be remarked that this method is usually

quite fragile[1]. Indeed it is very hard to generate an infinitesimally short signal

and capture a very small measurement where the noise of the sensor can be

dominating.

Due to the fragility of the first attempt, a second try was done using the step

response as shown in fig.23

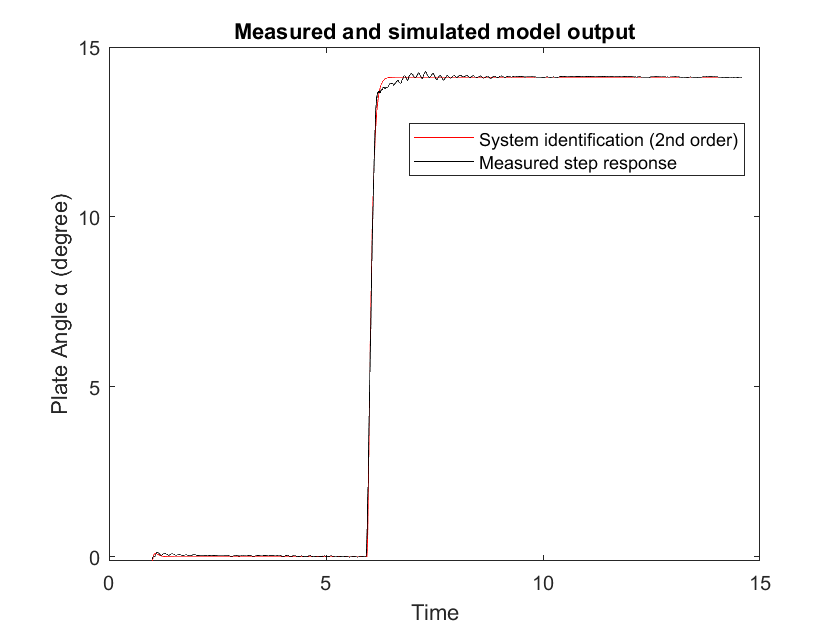
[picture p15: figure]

Figure 23: System identification using step response (a step of 80 degree is used

here to reach the maximum actuator angle).

for the sake of completeness, a third attempt of identification was done with the

unitary step response.

33

Design and Control of a Ball and Plate Didactic Device | MA2-MECA

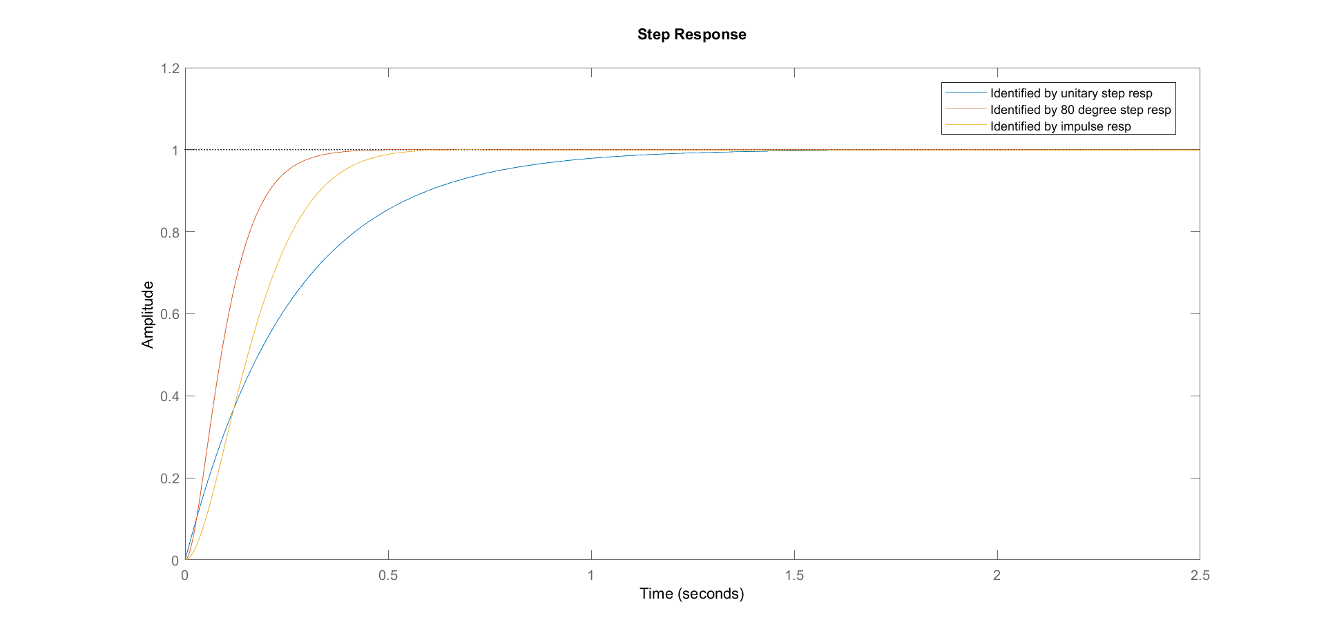
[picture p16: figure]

Figure 24: Unitary Step response of the three identifications.

Remark: Notice in fig.24 that each of the attempts identified a different transfer

function for the same system. If other types of input signals like a triangular or

sinusoidal signal was used, other aspect of the non linear plant will show. This

difference is not just due to the unreliable measurement and sensor noise, it is also

because the behavior around the origin is different than around a high operating

point. This latter observation is not only because of the static friction (stiction)

but also the servo’s internal controller that is more sensible to big references than

a small one.

Since we’re interested in having a linearized system, we should try to avoid the

static friction region very close to the origin. In this way we can have a clear

identification of the linear zone. To achieve this, a step input was given to break

the static friction before commencing the identification as shown in fig.25.

34

Design and Control of a Ball and Plate Didactic Device | MA2-MECA

Figure 25: System identified by avoiding the static friction

Obtaining the transfer function in the form of C.ω² n
s
| 2+2.ζ.ωn.s+ω²
n

, one can directly

determines the parameters ωn and ζ to be successively 18rad/s and 1.

Remark: Note that the retrieved parameters are almost the same as the parame-

ters assumed without measurements, this is a good indication that the real plant

is built correctly. However, all of the perturbation in the signal was treated as

a sensor noise and was filtered, but in reality, a big portion of it is due to the

vibration. Not including these vibrations in the equation of motion is like ignoring

some of the system’s dynamics and might cause problems later on in the final

validation test.

### 3.3 Control System Design

### 3.3.1 States of Equilibrium:

Reminder: A state of equilibrium with respect to a constant input u¯ is a con-

figuration xe of the system such that:

•

¯f(xe, u¯) = 0 in continuous time

35

Design and Control of a Ball and Plate Didactic Device | MA2-MECA

•

¯f(xe, u¯) = xe in discrete time

where:

- x˙ = ¯f(x, u) in continuous time
- x(t + 1) = ¯f(x, u) in discrete time [1]

In order to determine the states of equilibrium of our system :

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
(21)

xḃ

5/7(

−fc
mb

xḃ − g sin α)

α˙

−2ζωnα˙ − ω

2
nα

=

0

0

0

0

(22)

by solving this equality, we will find that there is an infinite states of equilibrium

where xb can be any real number while all the other states are equal to zero. In

other words, x¯ is a state of equilibrium if the following is true: (xb ∈ IRn
)∩( ẋb =
0) ∩ (α = 0) ∩ ( ˙α = 0).

Remark: The latter outcome physically means that any position on the plate is

an equilibrium point as long as the velocity of the ball, the angle of the plate

and the angular velocity of the plate are zero. However, in reality, the plate has

boundaries which means that only the equilibrium states bounded by the plate’s

area are valid.

Since there is an infinite number of equilibrium points, it is impossible for the

equilibrium points to be globally attractive. And for the local attractivity, we

36

Design and Control of a Ball and Plate Didactic Device | MA2-MECA

know that a non-empty neighborhood of xe for which the state converges to xe

does not exist. Therefore, non of the equilibrium points are locally attractive.

### 3.3.2 Stability Analysis:

Reminder: Based on the notion of stability and asymptotical stability (intro-

duced in the reference book [1]), in order for an equilibrium state to be stable,

any ball of radius > 0 in which we want to confine the whole state trajectory,

we can find a ball of initial states around the equilibrium such that the trajectory

will not go outside a ball of radius δ > 0.

Based on the stated definition of stability, non of the equilibrium states is stable.

Based on the BIBO stability definition, if a system gives a bounded output for

any bounded input then it is BIBO stable. In our system, any bounded input

angle α will cause the state xb to go to infinity, Hence the system is not BIBO

stable. This can be proven by looking at the transfer function obtained by the

laplace transformation:

G(s) = Y (s)
U(s)

=

Xb(s)
α(s)

=

2507
s

4 + 38.47s

3 + 369.6s

2 + 111.1s

The roots of the corresponding characteristic polynomial are:

s1 = 0

s2 = −21.5800

s3 = −16.5791

s4 = −0.3106

Note that, s1 is zero and therefore, not all the poles of the system have a negative

real part. This means that the system is not BIBO stable.

37

Design and Control of a Ball and Plate Didactic Device | MA2-MECA

After replacing all of the parameters in the state space with their real numbers

and choosing the 4th ball configuration we get:

xḃ

x¨b

α˙

α¨

=

0 | 1 | 0 | 0
0 −0.3106 | 7.007 | 0
0 | 0 | 0 | 1
0 | 0 | −357.8 −38.16

xb

xḃ

α

α˙

+

0 0 0 357.8
αr

(23)

As an LTI system, the stability depends only on the eigen vector of the matrix

A:

eig(A) =

0

−0.3106

−16.5791

−21.5800

(24)

Now that we know the system is unstable, the question is "can we stabilize

the system ?". To answer this question, we should first check if the system is

controllable or not.

### 3.3.3 Controllability Analysis:

As previously defined, the controllability matrix corresponding to our system is:

R =

B AB A²B A³B
=

0 | 0 | 0 | 2506.99
0 | 0 | 2506.99 | −96443.34
0 | 357.77 | −13652.46 | 392961.5
357.77 −13652.46 | 392961.5 | −10110524.55

This controllability matrix is full rank (rank(R) = 4), this means that the system

38

Design and Control of a Ball and Plate Didactic Device | MA2-MECA

is controllable and therefore, theoretically, any eigen value can be manipulated

arbitrarily to reach the desired behavior.

### 3.3.4 Observability Analysis:

Reminder: The observability is the ability to fully estimate the states given a

certain configuration of sensor measurement. Just like in controllability, if the

observability matrix is full rank then the system is observable. Note that this

definition is precisely for the critical states and not useless states in the state

vector, therefore, this definition is only valid for the minimal realization of the

state space.

Our system has the following observability matrix:

O =

C

AC

A²C

A³C

=

1 | 0 | 0 | 0
0 | 1 | 0 | 0
0 −0.31 | 7 | 0
0 | 0.09 | −2.17 7

The system is observable since the matrix O is full rank (rank(O) = 4). This

means that we can estimate all the states from the displacement measurement.

Bear in mind that if we chose to measure exclusively the velocity of the ball,

the angle of the plate or the angular velocity of the plate, the new C matrix

will render the observability matrix O non full rank which means that the system

would not be observable. (this proves that choosing only one sensor for the ball

displacement is enough.)

39

Design and Control of a Ball and Plate Didactic Device | MA2-MECA

### 3.3.5 Control Requirements:

Now that we know the system needs to be stabilized, the first task is to indicate

the control requirements. The requirements will put the foundations and con-

straints needed to come up with a good controller. A reasonable requirement

list for a step response is as follows:

- settling time : 4% ts ≤ 3s
- overshoot : ≤ 20%
- steady state error : ≤ 5mm
- Gain margin ≥ 10db
- phase margin ≥ 45 deg

### 3.3.6 Control Design and Simulation:

To design a controller that fulfill the stated requirements, the most common

ways do so is by:

- Pole placement (using the root locus)
- Loop shaping (using bode plot)
- Automatic tuning by simulink

As a first attempt, we will be using the robust feedback scheme with a PID

controller. The block diagram is arranged as shown in fig.26.

40

Design and Control of a Ball and Plate Didactic Device | MA2-MECA

Figure 26: Simple closed feedback loop

With such requirements, root locus can be the simplest tool to design the con-

troller.

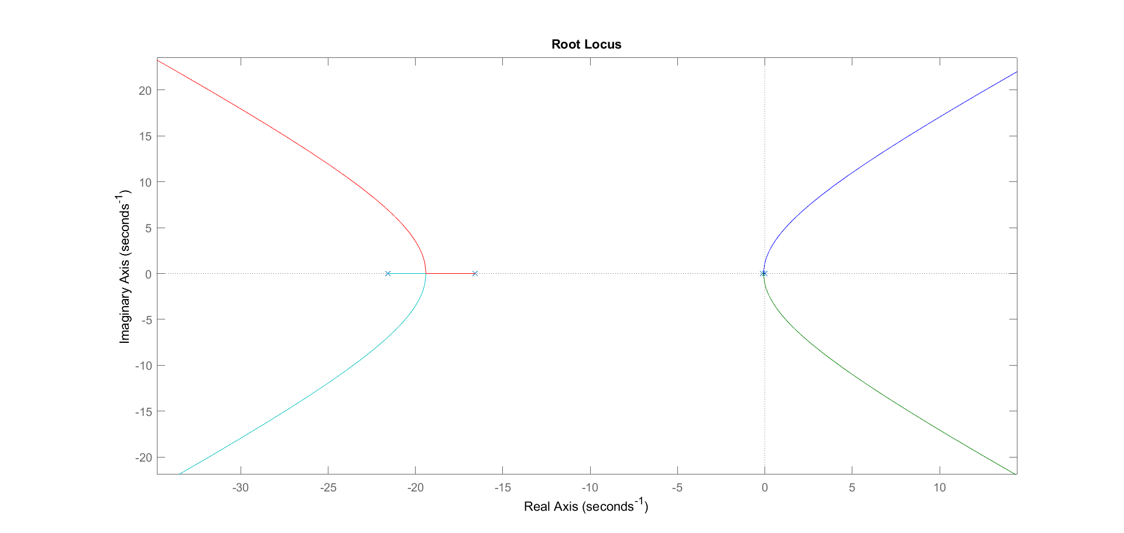
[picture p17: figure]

Figure 27: Corresponding root locus with no controller

From the root locus plot shown in fig.27, it is clear that the system is not BIBO

stable and that there is 2 dominant poles that are very close from the real axis that

needs to be damped. By closing the loop and applying a small proportional gain,

the system is stabilized, however, it is far from fulfilling the control requirements

and it has poor stability margins.

41

Design and Control of a Ball and Plate Didactic Device | MA2-MECA

Since the plant is a 4th order system, the 2nd order formulas for placing the

poles in a region where the requirements can be fulfilled doesn’t work. However,

the system can be treated as a second order as long as the 2 damped poles are

reasonably far and don’t contribute much to the dynamics of the system.

By using the 2nd order overshoot formula [2]:

Mp = e

−πζ/

√
1−ζ

2

Where Mp is the overshoot and ζ is the damping ratio of the second order

system. For an overshoot Mp ≤ 10%, ζ ≥ 0.6. A bounded ζ region can be

constrained on the root locus where the angle of the dominant poles shouldn’t

exceed sin⁻¹ ζ.

Another region can be ploted for the settling time where ts =

4.6
ζωn

=

4.6
σ ≤ 3,

thus the real part of the dominant poles shouldn’t exceed σ.

By applying only a PD controller with a low pass filter (lead compensator) as

shown in fig.28, the pole cancellation method can cancel one of the dominant

poles and make the new dominant poles fit in the constrained region. The step

response of the controlled plant is shown in fig.29. Bear in mind that using a

PID with an integrator or using a lag compensator instead of a lead will place

a third pole close to the real axis which will make the stability circumstances

worse.

42

Design and Control of a Ball and Plate Didactic Device | MA2-MECA

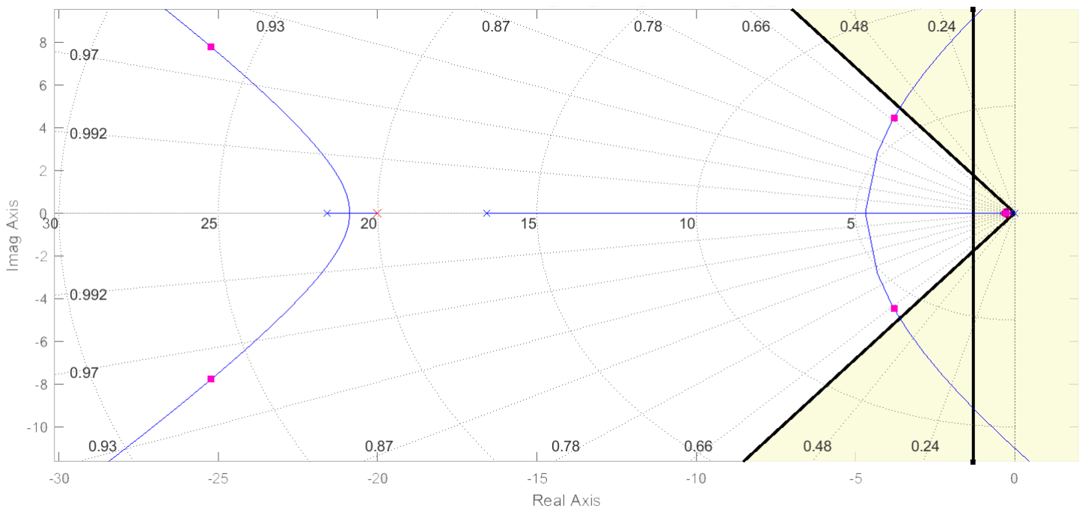
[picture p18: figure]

Figure 28: PD controller to fulfill the requirements

Figure 29: Step response of the plant by the aggressive PD controller.

The obtained PD controller also fulfills the gain and phase margins required, this

can be seen in fig.30 where the margins are successively 11.8db and 110 deg.

Note that There is a clear physical interpretation that could be obtained from

the bode plot which shows that the system is a low pass filter where the ball rolls

normally whenever the angle of the plate is tilted with low frequencies, but with

higher frequencies, the ball’s displacement is reduced and also lagging the angle

43

Design and Control of a Ball and Plate Didactic Device | MA2-MECA

of the plate until full stop.

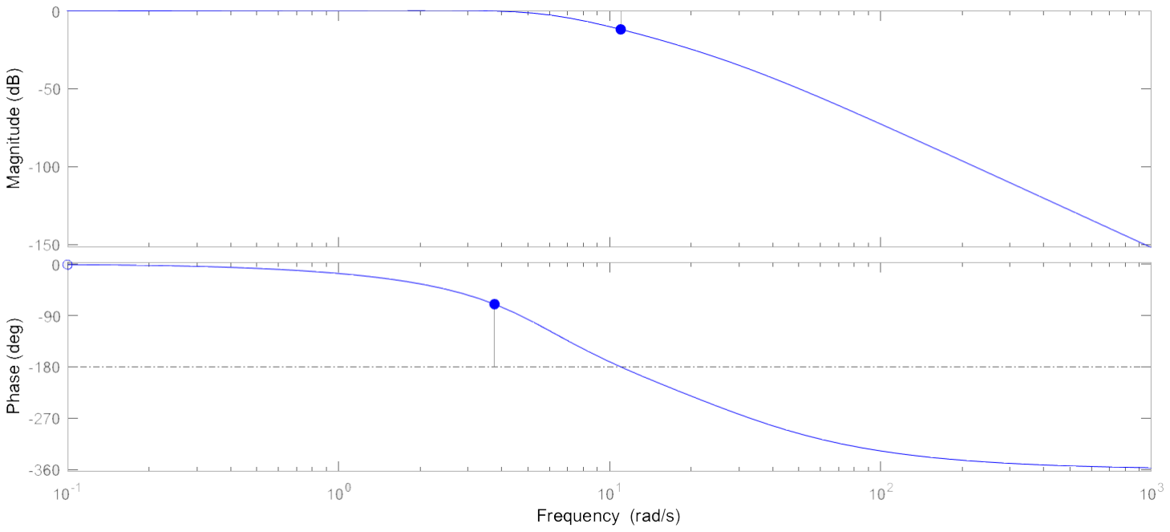
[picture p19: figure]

Figure 30: Bode plot using the obtained PD controller.

Remark: In practice, the locations of the lightly damped poles are not known

precisely and exact cancellation is not really possible. However, placing the zero

near the locations of the lightly damped poles may provide sufficient improvement

in step response performance. Note that one must avoid unstable cancellations.

[2]

In reality, the latter controller won’t perform similarly. One of the major reasons

why is that the actuators are saturated which means that the plate can only be

tilted to a limited angle of ±15 deg. However, this can be verified by applying

the controller to the non linear model as shown in fig.31.

44

Design and Control of a Ball and Plate Didactic Device | MA2-MECA

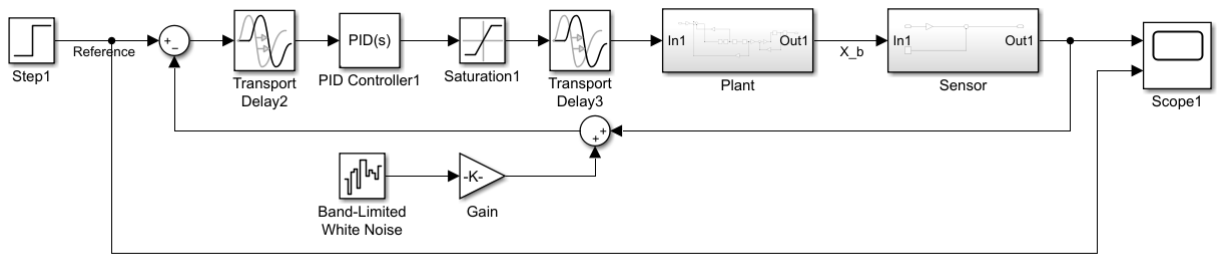
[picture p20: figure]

Figure 31: continuous time simulink model

Remark: Notice the sensor block used after the plant, it is used to map the

values of the displacement from the world frame to the sensor’s reference frame

which has pixels as coordinates. On the other hand, two delay blocks are used

to imitate the image processing delay and the command transport delay from

the computer to the arduino. A saturation block is used after the controller to

saturate the actuator’s angle. Furthermore, a sensor noise is also added to the

model.

In reality, the current model still doesn’t hold true since the sampling time of

the discrete controller can alter the behavior drastically. Therefore, another

simulation model has been obtained by discretizing as shown in fig.32.

Figure 32: discrete time simulink model

Remark: Notice the zero order hold blocks added to model the sampling time

45

Design and Control of a Ball and Plate Didactic Device | MA2-MECA

of the sensor ( camera is capturing 30 FPS⁷
, which gives a sampling time ts =

0.033s). There is another ZOH⁸ block to model the arduino’s discrete output

signal.

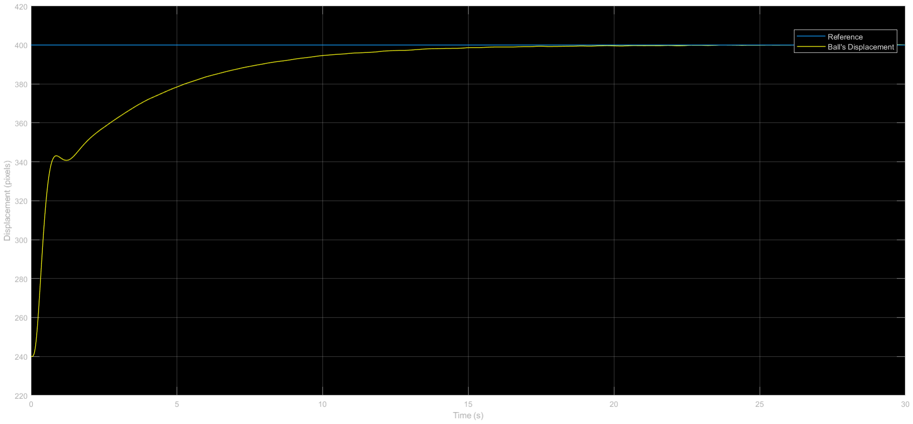
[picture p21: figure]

Figure 33: Reference tracking using the obtained PD controller on the final

discrete non linear system.

The performance shown in fig.33 Doesn’t comply at all with the settling time

expected. This behavior could be justified by looking at the controller’s command

shown in fig.34.

7Frames per second
8The zero-order hold is a mathematical model of the practical signal reconstruction done

by a conventional digital-to-analog converter.

46

Design and Control of a Ball and Plate Didactic Device | MA2-MECA

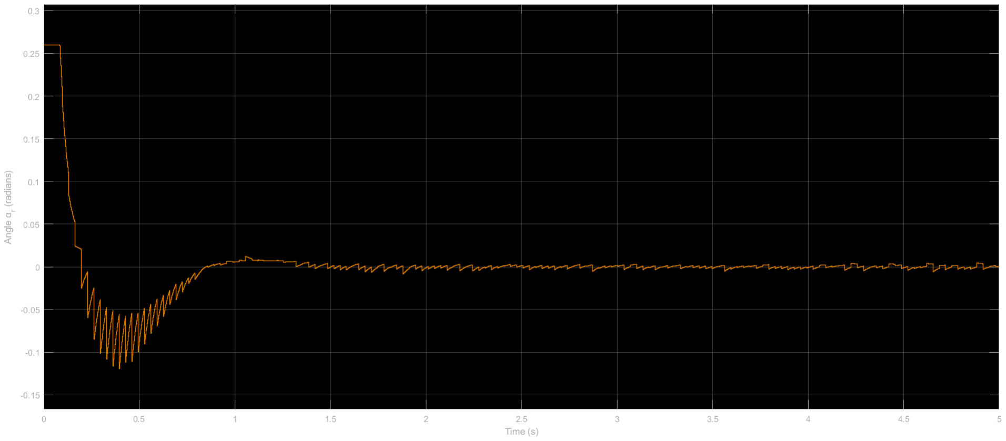
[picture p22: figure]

Figure 34: Controller command saturated at 0.26rad (14.9 deg)

Even though the obtained controller was not as good as intended, it was one

step closer to the solution. So using the same approach, a better controller was

obtained in fig.35. Manual tuning is totally okay once the designed controller is

close enough from what is requested.

Figure 35: Reference tracking using the perfectly tuned PD controller with the

Parameters(P = 0.03, D = 0.02, N = 20)

47

Design and Control of a Ball and Plate Didactic Device | MA2-MECA

Note that the N stands for the cuttoff frequency in (rad/s) of the first order low

pass filter implemented in the derivatrive action to filter out the sensor noise and

vibrations. Multiple ways to show the low pass filter are shown in fig.36 where

all of these branches gives the same result.

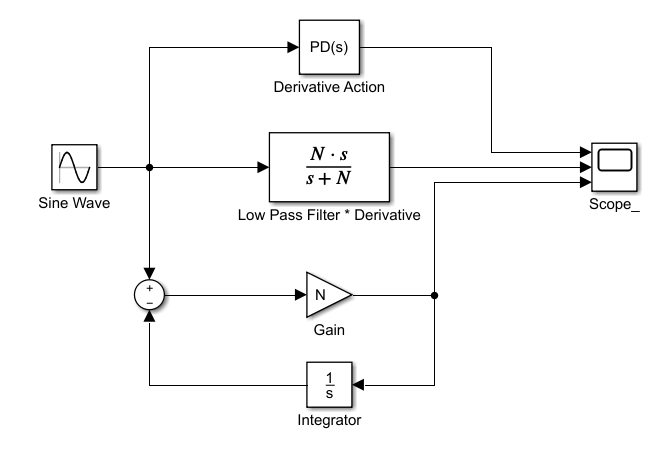
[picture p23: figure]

Figure 36: Multiple ways to implement the low pass filter on the derivative action.

The goal of showing fig.36 is to emphasize that implementing the Derivative

action in the python source code can be done in two ways. An integral in the

feedback loop is a much efficient way in terms of memory and logical operation.

## 4 Results and Validation

Now that a good controller has been designed and tested by simulation on the

discrete non linear model, It is time to validate the performance on the real plant.

48

Design and Control of a Ball and Plate Didactic Device | MA2-MECA

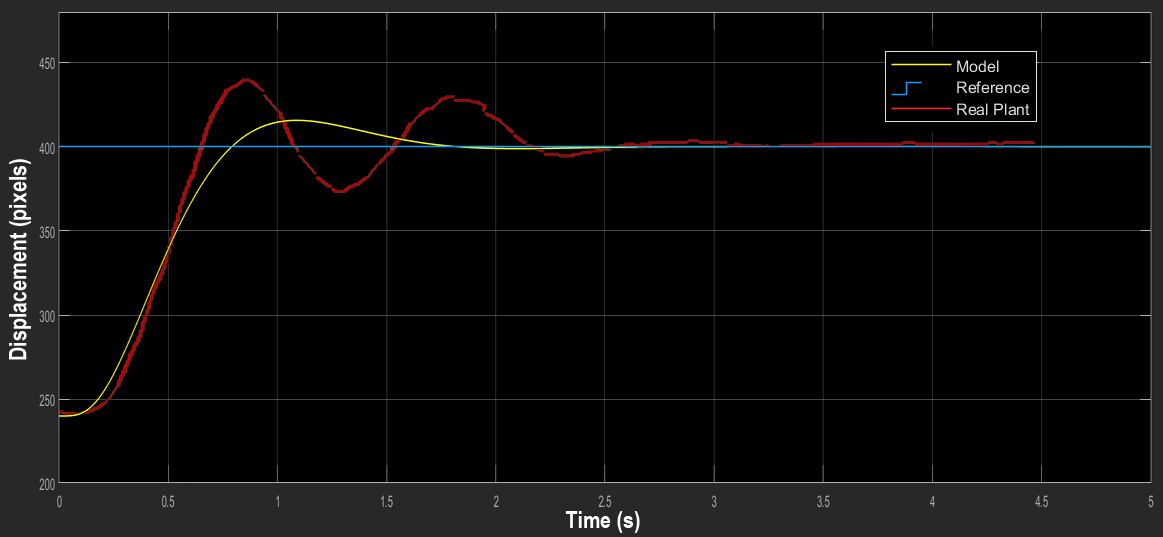
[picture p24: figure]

Figure 37: Performance on the real plant(P = 0.03, D = 0.02, N = 20)

Using the same controller, the comparison with the real plant shown in fig.37

elaborates that the model is still different from the real plant. This difference can

be for many reasons like not including the static friction, structural vibrations,

uncertainties in the time delay, variations in the noise and delays or perhaps

imperfections in the surface of the plate and ball. Going back to the model and

increasing the time delay results in a similar oscillatory behavior.

Being so close from capturing the real dynamics of the model, manual tuning

can be a faster way in achieving an optimal performance. By tweaking the PD

sliders in the GUI, a superior controller was obtained as shown in fig.38

49

Design and Control of a Ball and Plate Didactic Device | MA2-MECA

Figure 38: Comparison of performance for multiple PD controllers on the real

plant

Remark: Note that the steady state error can be eliminated by an integral action,

but since the error is small, a PD controller will suffice. The reason of the steady

state error is the static friction. Whenever the ball is so close from the desired

reference, a small angle tilt for the plate is not enough to break the static friction,

therefore, the ball get stuck with a steady state error.

The step response is always good to clearly see the quality of the controller’s

performance, however, the plant should be able to track any reference given to

it. The tracking of a sinusoidal reference is shown in fig.39.

50

Design and Control of a Ball and Plate Didactic Device | MA2-MECA


Figure 39: Tracking of a sinusoidal reference

Remark: The latter figure, shows an expected behavior. Using a PD controller

there will be always a delay in tracking moving references. However, there exists

many other controllers such as the repetitive and the resonance controllers which

are more adequate to track periodic references precisely and without delay.[3]

## 5 Discussion and Conclusion

So far, this study demonstrated a systematic way of developing and controlling

of the 2DOF Ball-Plate.

Choosing the controller structure is an important question. Since the system al-

ready has a double pole in the coordinate starting point, an additional integrator

pole would only make the stability circumstances worse, the usage of PID regu-

lator is not recommended. However, a PD controller with a low pass filter which

is actually a lead controller is relevant while a lag controller does not stabilize

the system. The usage of the PD controller has been established to be a good

51

Design and Control of a Ball and Plate Didactic Device | MA2-MECA

solution.

On the basis of the controlled system stability analysis and in combination with

the Pole placement and loop shaping techniques, good controller coefficient has

been derived and it has been confirmed as a successful tool to resolve the problem

described.

### 5.1 Problems and Possible Improvements

There exist many ways to improve the design of the plant and the controller.

The Results shown in this study were all based on the image processing using

the camera. Implementing a touch screen could have been simpler, however, the

noise and discontinuities in the readings were intolerable even after filtering, So

this touch screen approach had to be discontinued.

Another failure was imminent, the TURNIGY Servo used in this study was ac-

tually not the first choice. Another Servo motor was used before and had to be

changed since it had bad centering and a delay in the response.

The universal joints chosen in the mechanical design section had to be changed.

The small gap in the joint introduces a play which gives vibrations and allows

the plate to be tilted in one direction more than the other. The magnetic ball

joints eliminate these vibrations and Thus, remove some of the uncertainties.

The Camera pole was also badly designed in way that allows the weight of the

camera to bend the pole and Thus, It doesn’t have a good alignment over the

plate anymore. This problem was temporarily fixed by tying a rope on the camera

pole to correct the flexion.

The thin supporting structure of the camera allowed vibrations to reach and

52

Design and Control of a Ball and Plate Didactic Device | MA2-MECA

therefore introduced vibration noise in the readings. This problem could be fixed

by supporting the camera by two poles.

## References

[1] Prof. Emanuele Garone, Assistant Professor Faculté des Sciences Ap-

pliquées/école Polytechnique Université Libre de Bruxelles, Lecture Notes

of Control System Design - Discrete Time System Theory

[2] Gene F.Franklin, J.David Powell, Abbas Emami-Naeini - Feedback Control

of Dynamic Systems, Sixth Edition

[3] Rafael da Silveira Castro, Group of Automation and Control Systems –

PUCRS – Brazil, BALL AND PLATE SYSTEM

[4] Advanced | Micro | control | INC., | Stepper | vs | servo | -

https://www.amci.com/industrial-automation-resources/plc-automation-

tutorials/stepper-vs-servo/

[5] Mohsin Mohammad Taufiq, Dr. Chan Ham, Kennesaw State University -

122nd ASEE annual conference and exposition - Paper ID #12313, Devel-

opment of a Ball and Plate System

[6] Johan Link - Gymnase de Burier, Système de stabilisation PID
[7] Microchip - Atmel AVR341 document, AVR341: Four and five-wire Touch

screen Controller using tinyAVR and megaAVR devices

[8] Amor Chowdhury - University of Maribor, Modeling and control design for

the ball and plate system

53

Design and Control of a Ball and Plate Didactic Device | MA2-MECA

## Appendices

Since the Project files are so big to be placed in this study paper, a link is provided

to the open source Github repository of this project.

https://github.com/jihadsamarji/Ball-Plate-Control

The link provided contains the :

- CAD Files
- Source Codes
- Simulation files
- Pictures and Videos
- Supporting Documents and References
- Documentations on how to run the developed GUI.

The Files can be downloaded as a ZIP file. An alternative way to have the files

is also by cloning the git repository into your local machine.

54
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

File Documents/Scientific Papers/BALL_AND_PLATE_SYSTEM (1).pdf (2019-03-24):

# BALL AND PLATE SYSTEM

# Rafael da Silveira Castro


# Group of Automation and Control Systems – PUCRS – Brazil rafa.castro@brturbo.com.br

# 1. Prototype Overview

## A video of the prototype can be checked on:

## http://www.youtube.com/watch?v=N6IVamTIsLk

# 2. Material Description

## ( I ) - Acrylic plate

## ( II ) - Wood Base

## ( III ) - Hextronik HXT12K Servo-Motors. Available on:

http://www.hobbyking.com/hobbyking/store/__2__hxt_10kg_servo_metal_gear_55g_10kg_16sec.html

## ( IV ) - Arduino Prototyping Board (Mega 2560 or similar)

## ( V ) – Jacks for source cables

( VI ) , ( X ) and ( XI ) – Hollow Carbon Fiber Tubes (9mm /4mm diameters).

## Available on:

http://www.hobbyking.com/hobbyking/store/uh_viewItem.asp?idProduct=6723

## ( VII ) – USB Webcam (Microsoft VX-800 or similar)

## ( VIII ) and ( XII ) – Universal Joints. Available on:

http://www.ebay.com/itm/297c-1-set-U-Joint-D9-4-to-4-M3-L22mm-parts-for-RC-Boat/200940139345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 6asc%3D11%26meid%3D2490461304689761428%26pid%3D100011%26prg%3D1005%26rk%3D3%26rkt%3 D5%26sd%3D200960448149%26 (http://www.ebay.com/itm/297c-1-set-U-Joint-D9-4-to-4-M3-L22mm-parts-for-RC-Boat/200940139345)

## ( IX ) – Ball Roller Joints. Available on:

http://www.hobbyking.com/hobbyking/store/__8233__Ball_and_roller_link_3_9x2x16mm_10pcs_.html?strSearch=b all roller (http://www.hobbyking.com/hobbyking/store/__8233__Ball_and_roller_link_3_9x2x16mm_10pcs_.html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)

Remark 1: Recommended a PC with MALAB for controlling the plant.

Remark 2: The recommended sphere is a mouse ball.

# 3. Detailed Mechanical Project


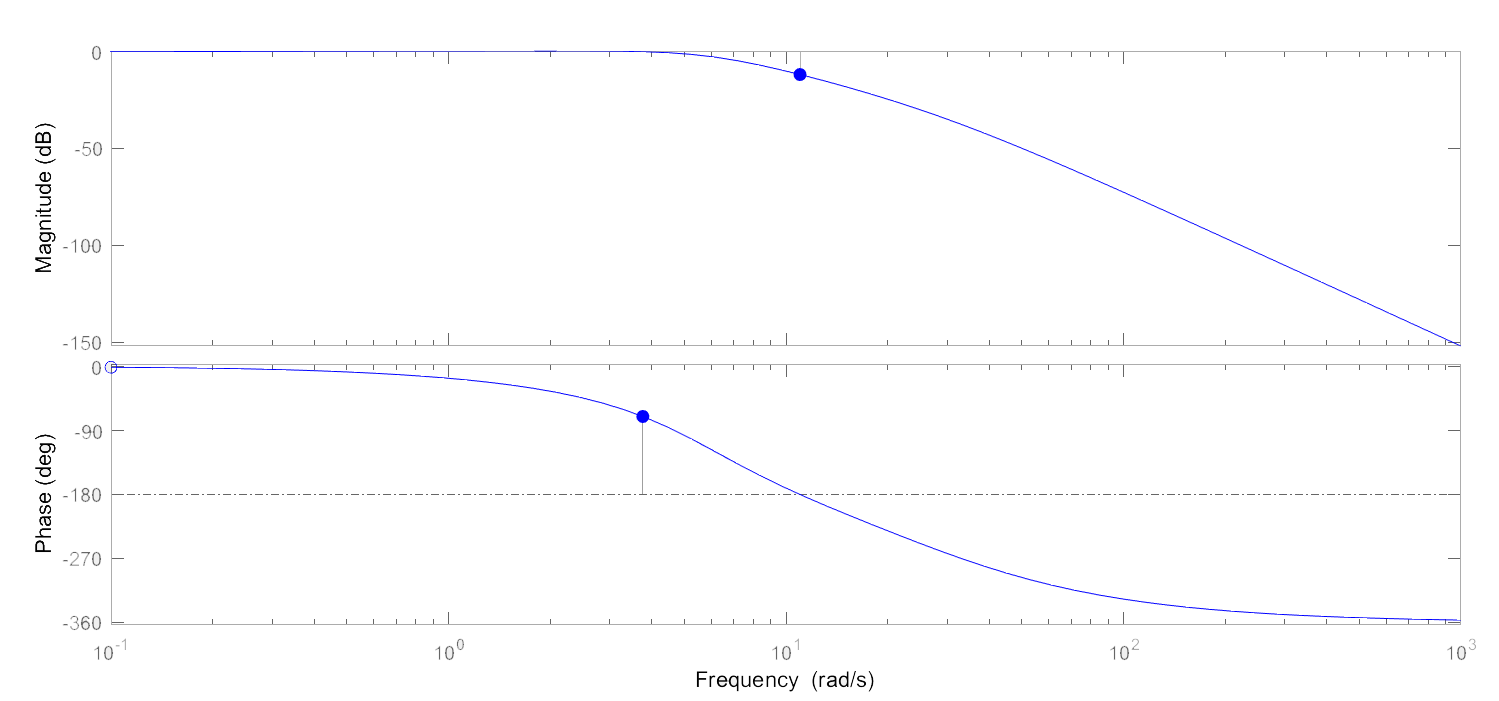
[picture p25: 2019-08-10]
Pictures/control design/bode.PNG

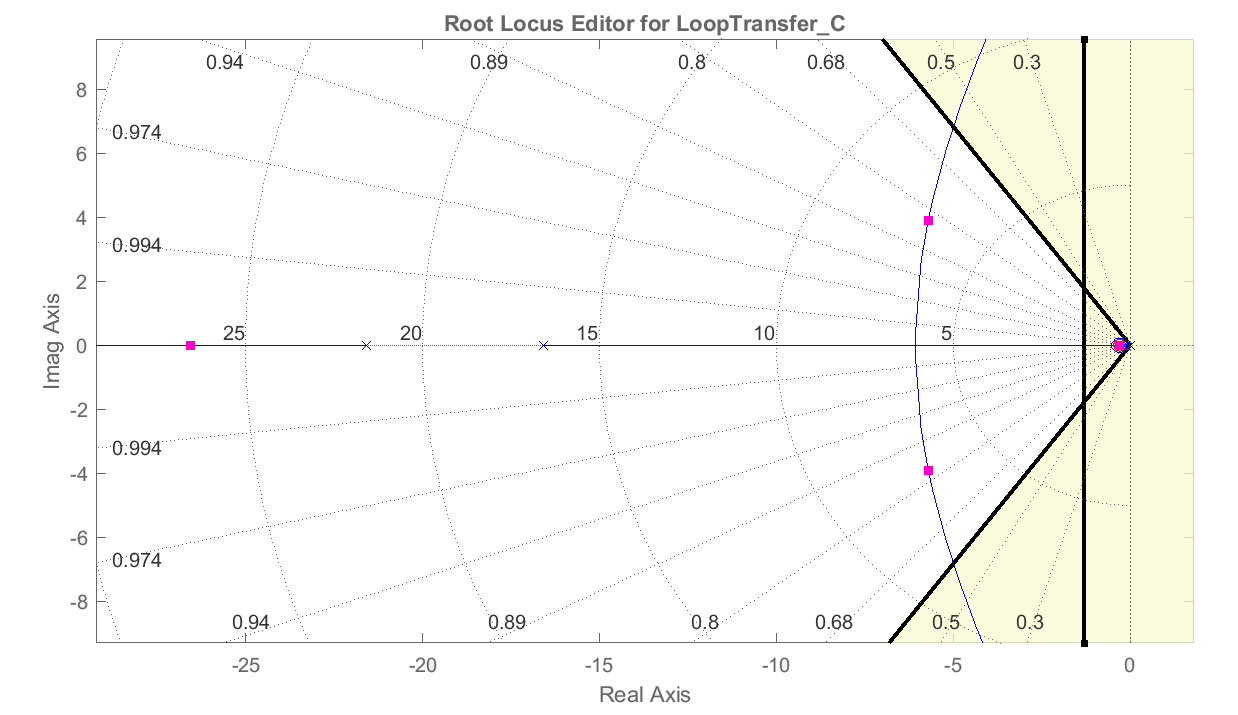
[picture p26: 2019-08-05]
Pictures/control design/PDrloc.PNG

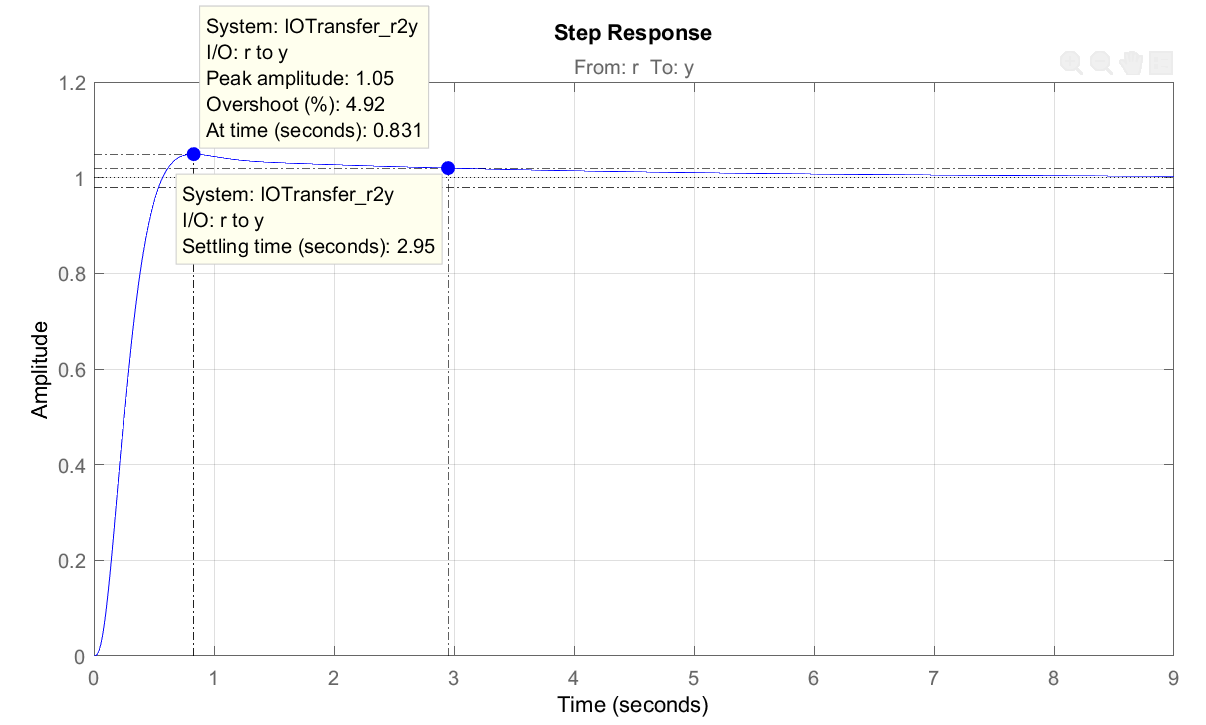
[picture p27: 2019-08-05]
Pictures/control design/PDstepfake.PNG

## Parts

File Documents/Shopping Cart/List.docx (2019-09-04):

I have prepared a list of Items to Purchase with their links and selection preferences.

- Arduino Uno (https://fr.aliexpress.com/item/high-quality-One-set-UNO-R3-CH340G-MEGA328P-for-Arduino-UNO-R3-NO-USB-CABLE/32697443734.html) ( Quantity: 1) [ Link selection : 1 ]

- Arduino Uno (https://fr.aliexpress.com/item/high-quality-One-set-UNO-R3-CH340G-MEGA328P-for-Arduino-UNO-R3-NO-USB-CABLE/32697443734.html) Usb Wire ( Quantity: 1) [ Link selection : 2 ]

- Electrical Harness (https://www.aliexpress.com/item/Dupont-Jumper-Wire-10CM-20CM-30CM-for-Arduino-Breadboard-Cable-Line-Male-to-Male-Male-to/32911287776.html) ( Quantity: 1) [ Link selection : 8 ]

- Ball roller joints (https://fr.aliexpress.com/item/Ball-Head-Holder-Tie-Rod-End-3mm-Hole-M4-4mm-Thread-25mm-Length-Link-Rod-End/32659618985.html) M4 ( Quantity: 2) [ Link selection : 1]

- Servo (https://fr.aliexpress.com/item/1-pi-ces-MG946R-mise-niveau-RC-Metal-Gear-Torque-Servo-Pour-Bateau-DE-VOITURE-13/32854187745.html)s ( Quantity: 2) [ CAUTION : this servo doesn’t work, use Turnigy TGY-4409MD]

- USB Camera (https://fr.aliexpress.com/item/100-Degree-No-distortion-Lens-High-speed-30fps-60fps-120fps-Webcam-HD-1080P-Android-Linux-Windows/32736010155.html) High speed ( Quantity: 1)

- 4 wires resistive touchscreen (https://fr.aliexpress.com/item/11-3-pouce-243-185-4-3-cran-carr-4113001-r-sistance-cran-tactile-livraison-gratuite/32841260011.html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) 11.3 inch ( Quantity: 1) [ CAUTION : this touchscreen is too noisy and doesn’t work on this plant. Find another one if you’re interested to use touchscreens instead of a camera]

- Ball roller joints (https://fr.aliexpress.com/item/2-2-3-3-3-17-4-5-6-8-10mm-Bateau-En-M-tal-Cardan/32923183417.html) 4mm to 4mm ( Quantity : 2 ) [ Link Selection: 14]

- Ball roller joints (https://fr.aliexpress.com/item/2-2-3-3-3-17-4-5-6-8-10mm-Bateau-En-M-tal-Cardan/32923183417.html) 4mm to 8mm ( Quantity : 1 ) [ Link Selection: 17]

- Carbon Fiber Tubes (https://fr.aliexpress.com/item/Ormino-3K-Carbon-Fiber-Tube-for-Drone-diy-Quadcopter-Frame-arm-Landing-Gear-6mm-8mm-10mm/32822916583.html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) 8mmx6mmx500mm ( Quantity : 1 ) [ Link Selection: 2]

- Carbon Fiber Tubes (https://fr.aliexpress.com/item/ORC-3-k-Fiber-De-Carbone-Tube-6mm-8mm-10mm-12mm-14mm-15mm-16mm-RC-Drone/32856131367.html) 6mmx4mmx500mm ( Quantity : 1) [ Link Selection: 1]

- Carbon Fiber Tubes (https://fr.aliexpress.com/item/4pcs-lot-New-Carbon-Fiber-Tube-3K-for-Quadcopter-Multicoptor-3mm-4mm-5mm-7MM-1-meter/32325154808.html) 4mmx3mmx500mm ( Quantity : 1 ) [ Link Selection: 2]

- Plexi Glass S (https://fr.aliexpress.com/item/1-pi-ces-2-10mm-Epaisseur-Effacer-Acrylique-feuille-de-plexiglas-Coupe-En-Plastique-Transparent-Conseil/32969283608.html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)heet 40cmx30cmx0.4cm ( Quantity : 1 ) [ Link Selection: 11]

- Knob (https://www.aliexpress.com/item/WAVGAT-Rotary-Encoder-Module-for-Arduino-Brick-Sensor-Development-Round-Audio-Rotating-Potentiometer-Knob-Cap-EC11/32915420023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) ( Quantity : 3 )

- Ball Glass 16mm ( Quantity : 1 )

- Ping Pong Ball White (https://www.aliexpress.com/item/10Pcs-Wholesale-Ping-Pong-Balls-Table-Tennis-Balls-Ping-pong-Pingpong-White-Balls-Chinese/32907991241.html) ( Quantity : 1) [ Link Selection: 1]

- Ping Pong Ball Orange (https://www.aliexpress.com/item/10Pcs-Wholesale-Ping-Pong-Balls-Table-Tennis-Balls-Ping-pong-Pingpong-White-Balls-Chinese/32907991241.html) ( Quantity : 1) [ Link Selection: 2]

- Stainless Steel Ball 38mm (https://www.aliexpress.com/item/304-Stainless-Steel-Hollow-Ball-Seamless-Sphere-Mirror-Ball-Home-Garden-Decoration-Supplies-Yard-Park-DIY/32912355232.html) ( Quantity : 1) [ Link Selection: 2]

- L Corner Bracket (https://www.aliexpress.com/item/10-pcs-2-Holes-Strong-Inside-Corner-Bracket-Gusset-for-3030-Series-Aluminum-Extrusion-Profile-with/32889590986.html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) ( Quantity : 1 ) [ Link Selection: 1]

*I have been Careful in choosing Dimensions and Prices.

*I have Chosen Both a Camera and a Restive Touch screen to experiment with both.

*The Servo that i have chosen is more powerful than what is needed, but it is Very Cheap.

*I took into consideration that i will be using the Power supply in the lab and Also i assumed that all kind of screws are available in the lab so i didn't include them.

*Each of these items will come in different dates since they are from different sellers, but they will take at most 40 days.

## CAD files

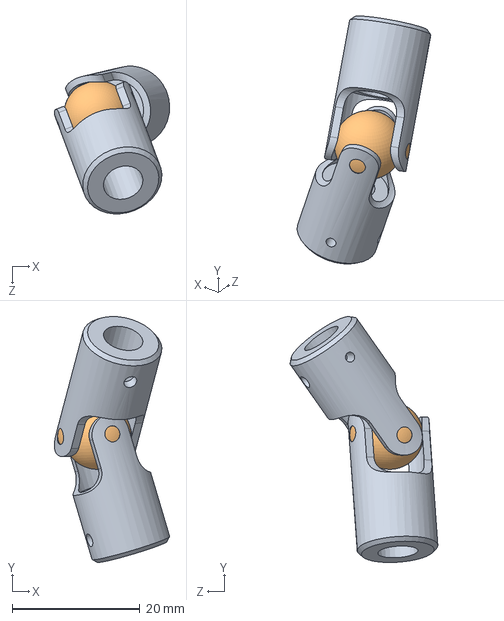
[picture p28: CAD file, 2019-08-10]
CAD/Assets/Universal Joint/1/ASSY_BERG_UJ3_U-JOINT_0250 SHAFT.sldasm
18.1 x 38.6 x 23.1 mm
UJ-3_YOKE x 2
UJ-3_BALL

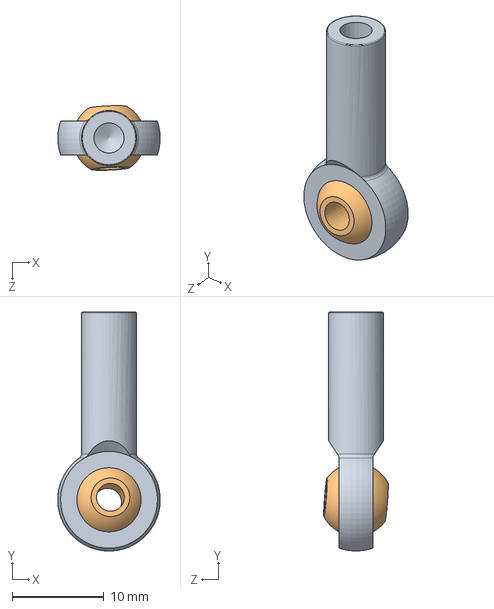
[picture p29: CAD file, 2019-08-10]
CAD/Assets/Ball joint/M4/M4 ball joint/M4_balljoint.SLDASM
11.2 x 26.1 x 7.07 mm
ball

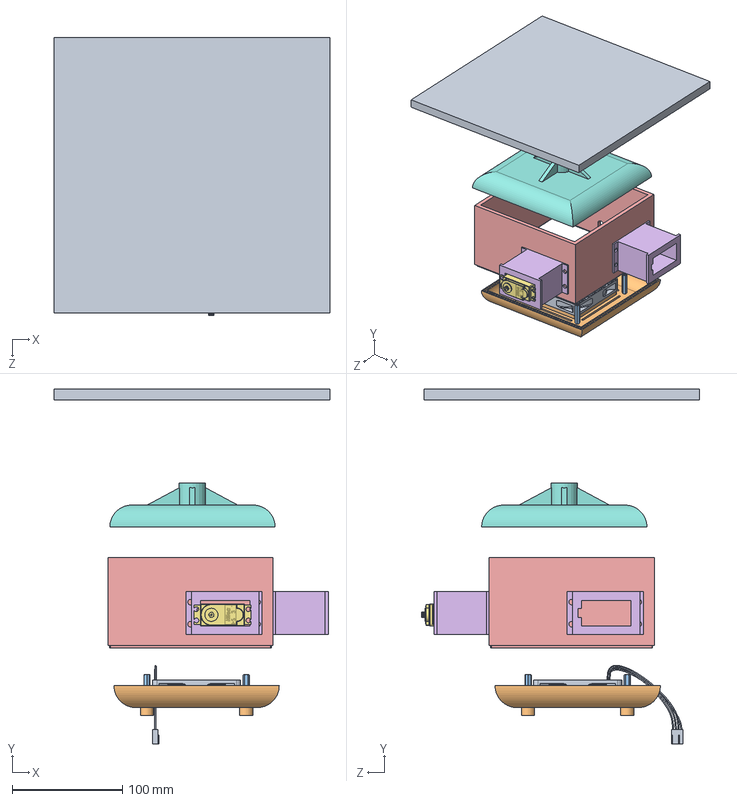
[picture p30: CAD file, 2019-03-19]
CAD/Thesis/Commercial/Final Assembly.SLDASM
250.0 x 322.0 x 252.2 mm
Exhaust Fan 80mm x 80mm x 15mm
Base
Hex Spacer FF M3 L25mm x 4
M3 pan Head x 10mm x 4
Servo mount 2 x 2
Hitec Servo Motor HS-311
TopCover
rectangular plate

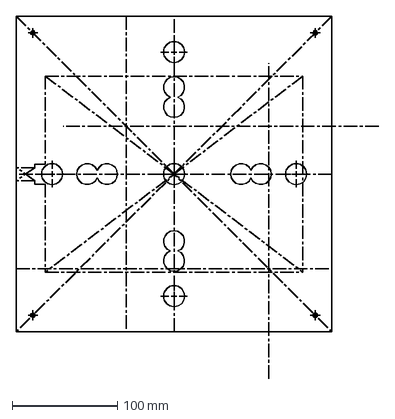
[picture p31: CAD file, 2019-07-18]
CAD/Thesis/Test Bench/Files for Laser Cutting/New Wooden Boards/Assembly Board.DXF
344.6 x 344.6 mm

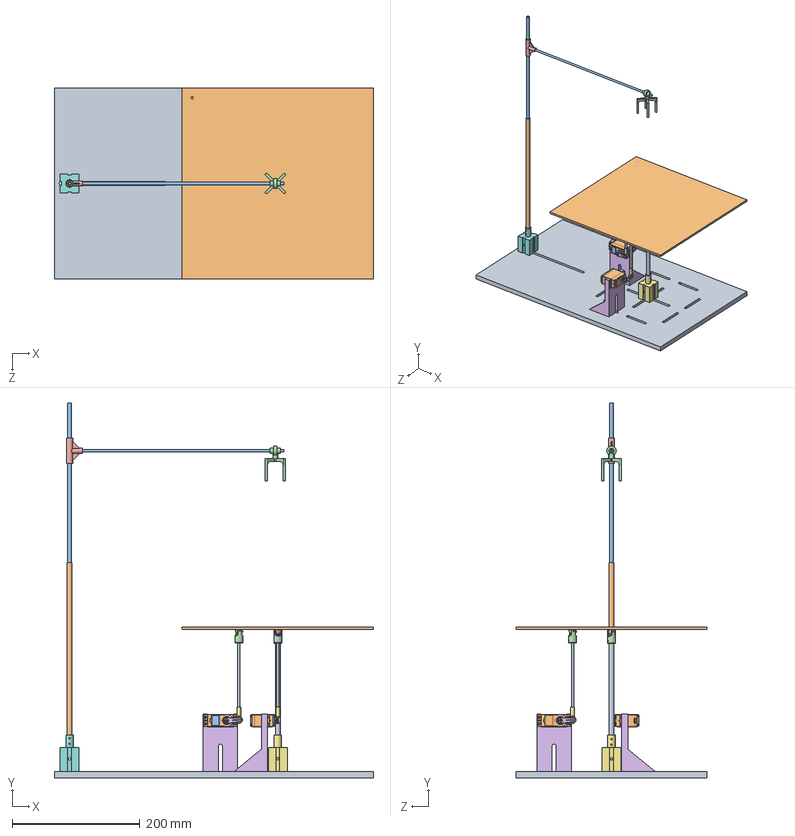
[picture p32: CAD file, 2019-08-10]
CAD/Thesis/Test Bench/Assem1.SLDASM
500.0 x 587.5 x 300.0 mm
Base
ROBOT SERVO Hitec HSR-2645CR x 2
ROBOT SERVO Hitec HSR-2645CR винт x 8
Servo_Mount_1 x 2
Center_Pole_Mount^Assem1
Copy of Camera_Pole_Mount
Center_pole^Assem1
Camera_pole_1^Assem1
Camera_pole_2^Assem1
UJ-3_YOKE x 3
UJ-3_BALL x 3
Copy of servo arm.prt^Assem1 x 2
ball x 2
Arm_1^Assem1 x 2
Plate
Part2^Assem1
Camera_Slider
T_Fit

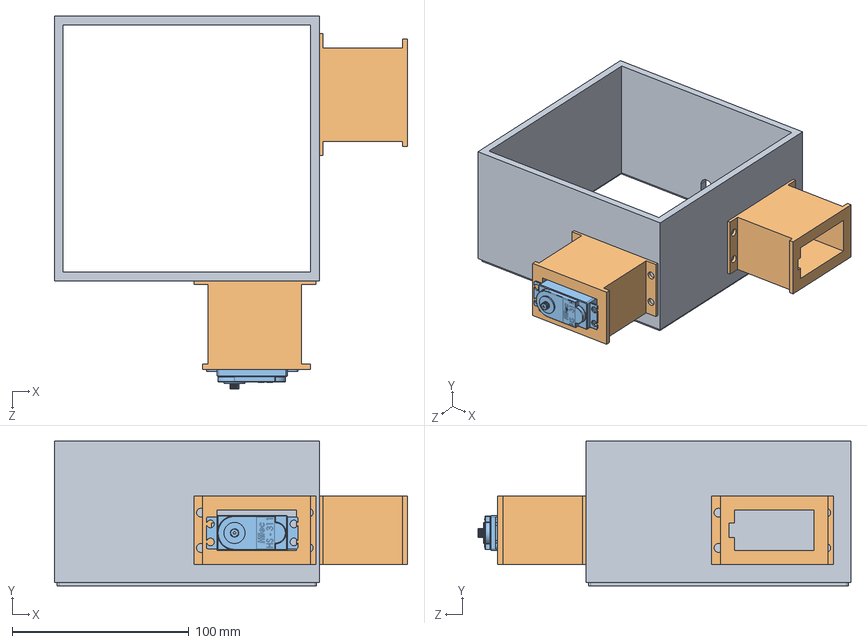
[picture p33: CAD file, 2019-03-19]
CAD/Thesis/Commercial/Box Assembly.SLDASM
200.0 x 82.0 x 211.1 mm
Servo mount 2 x 2
Hitec Servo Motor HS-311

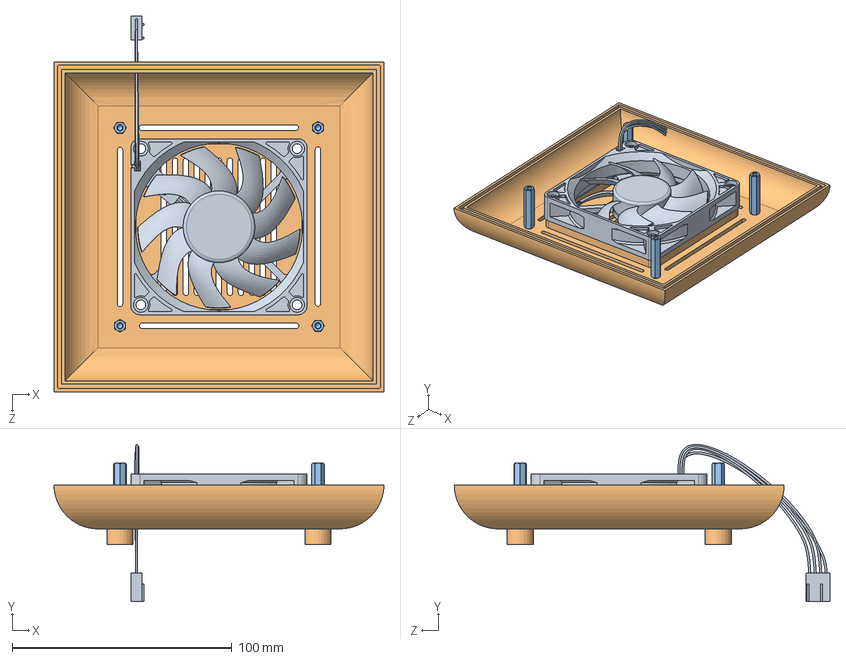
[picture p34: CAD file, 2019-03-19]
CAD/Thesis/Commercial/Assem.SLDASM
150.0 x 71.4 x 170.7 mm
Exhaust Fan 80mm x 80mm x 15mm
Base
Hex Spacer FF M3 L25mm x 4
M3 pan Head x 10mm x 4

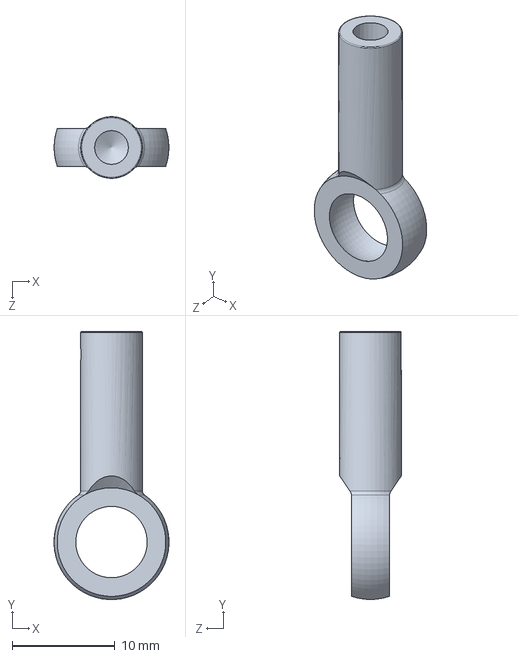
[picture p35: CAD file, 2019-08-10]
CAD/Assets/Ball joint/M4/M4 ball joint/body.SLDPRT
11.2 x 26.1 x 6.00 mm

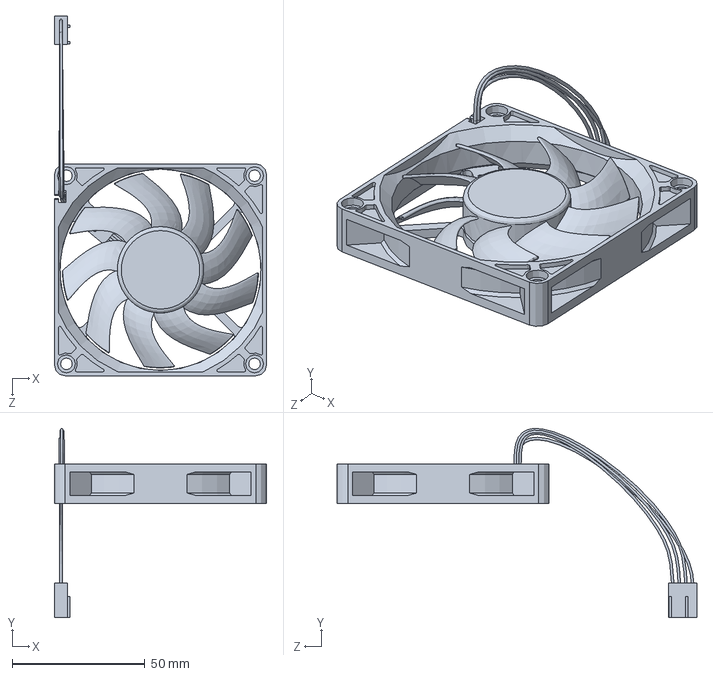
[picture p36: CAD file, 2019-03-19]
CAD/Assets/Fan 80x80x15/Exhaust Fan 80mm x 80mm x 15mm .SLDPRT
80.0 x 71.3 x 135.7 mm

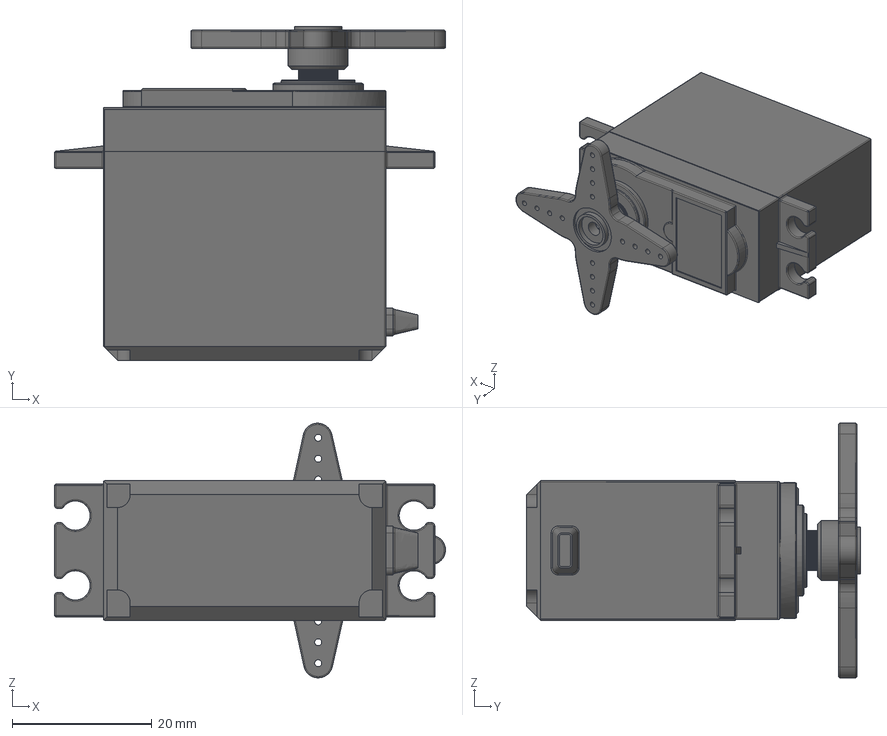
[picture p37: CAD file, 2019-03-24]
CAD/Assets/Futuba S3003 servo/2/Servo Futaba S3003 v6.step
56.0 x 47.8 x 36.5 mm

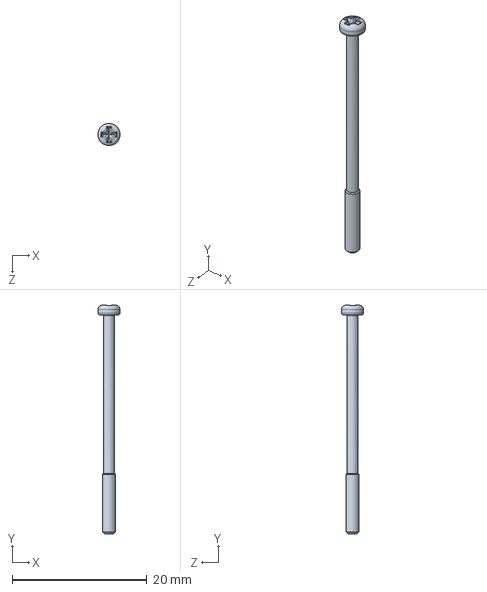
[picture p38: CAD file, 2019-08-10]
CAD/Assets/HiTec HS-785HB servo/ROBOT SERVO Hitec HSR-2645CR винт.SLDPRT
3.30 x 34.0 x 3.30 mm

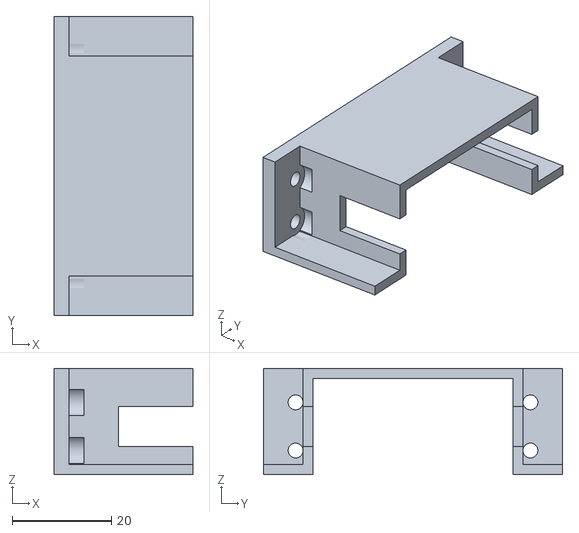
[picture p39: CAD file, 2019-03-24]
CAD/Assets/servo mounts/1/HS-5645MGN_NoHoles.stl
28.0 x 60.3 x 21.4

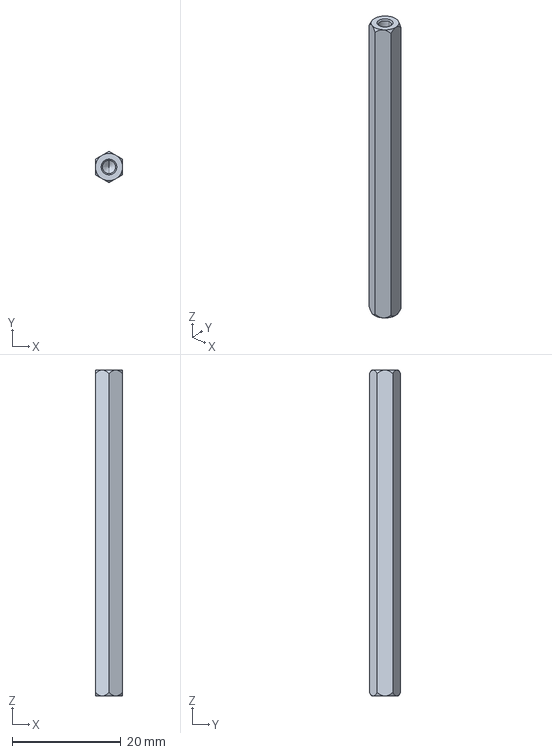
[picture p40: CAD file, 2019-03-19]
CAD/Assets/Spacers/M3 female female/Hex Spacer FF M3 L60mm.stp
5.00 x 5.77 x 60.0 mm

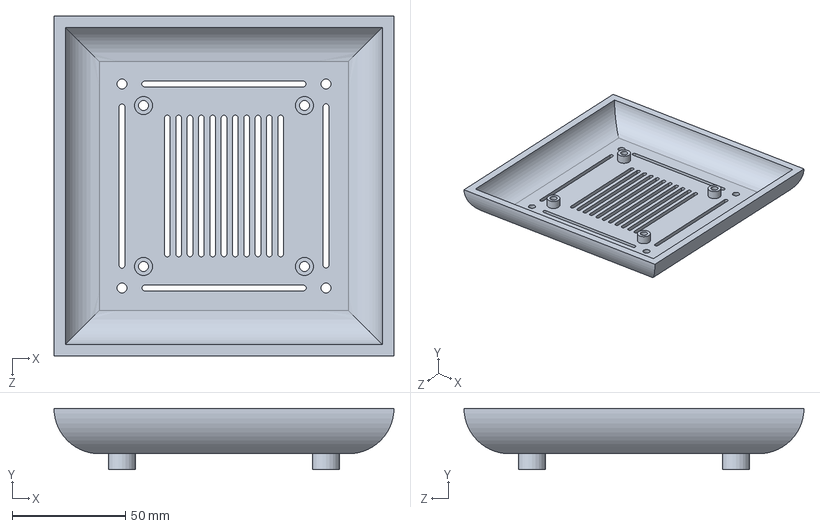
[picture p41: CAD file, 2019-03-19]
CAD/Thesis/Commercial/Base.SLDPRT
150.0 x 27.0 x 150.0 mm

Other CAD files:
CAD/Assets/Servo arm/2/Servo Arm HXT900 Micro.sldprt
CAD/Thesis/Test Bench/Files for 3d Print/Plug.STL
CAD/Thesis/Test Bench/Files for Laser Cutting/Base.SLDPRT
CAD/Thesis/Test Bench/Files for Laser Cutting/New Wooden Boards/Resistive_Board.DXF
CAD/Assets/Ball joint/M4/M4 ball joint/ball.SLDPRT
CAD/Assets/Futuba S3003 servo/2/Axis-holder v2.step
CAD/Assets/Futuba S3003 servo/2/Servo Futaba S3003 v6.iges
CAD/Assets/HiTec HS-785HB servo/01.SLDPRT
CAD/Assets/HiTec HS-785HB servo/02.x_t
CAD/Assets/HiTec HS-785HB servo/03.STEP
CAD/Assets/HiTec HS-785HB servo/ROBOT SERVO Hitec HSR-2645CR винт 2.SLDPRT
CAD/Assets/HiTec HS-785HB servo/ROBOT SERVO Hitec HSR-2645CR фланец.SLDPRT
CAD/Assets/HiTec HS-785HB servo/Наклейка сервы.SLDPRT
CAD/Assets/PSU/PSU assy.x_b
CAD/Assets/Screw/M3 5mm+10mm/M3 pan Head x 10mm.SLDPRT
CAD/Assets/Screw/M3 5mm+10mm/M3 pan Head x 5mm.IGS
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

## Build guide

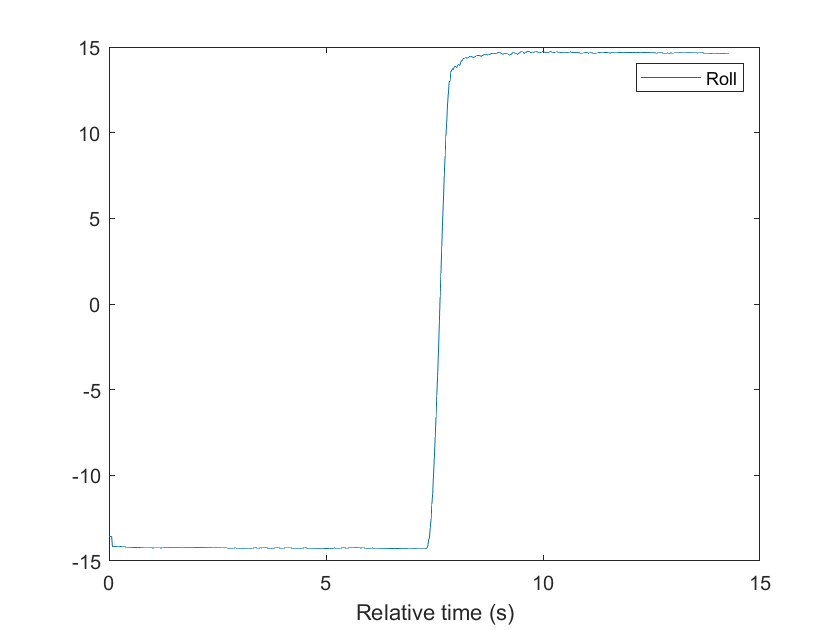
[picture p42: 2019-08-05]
Pictures/identification/servo(step).png

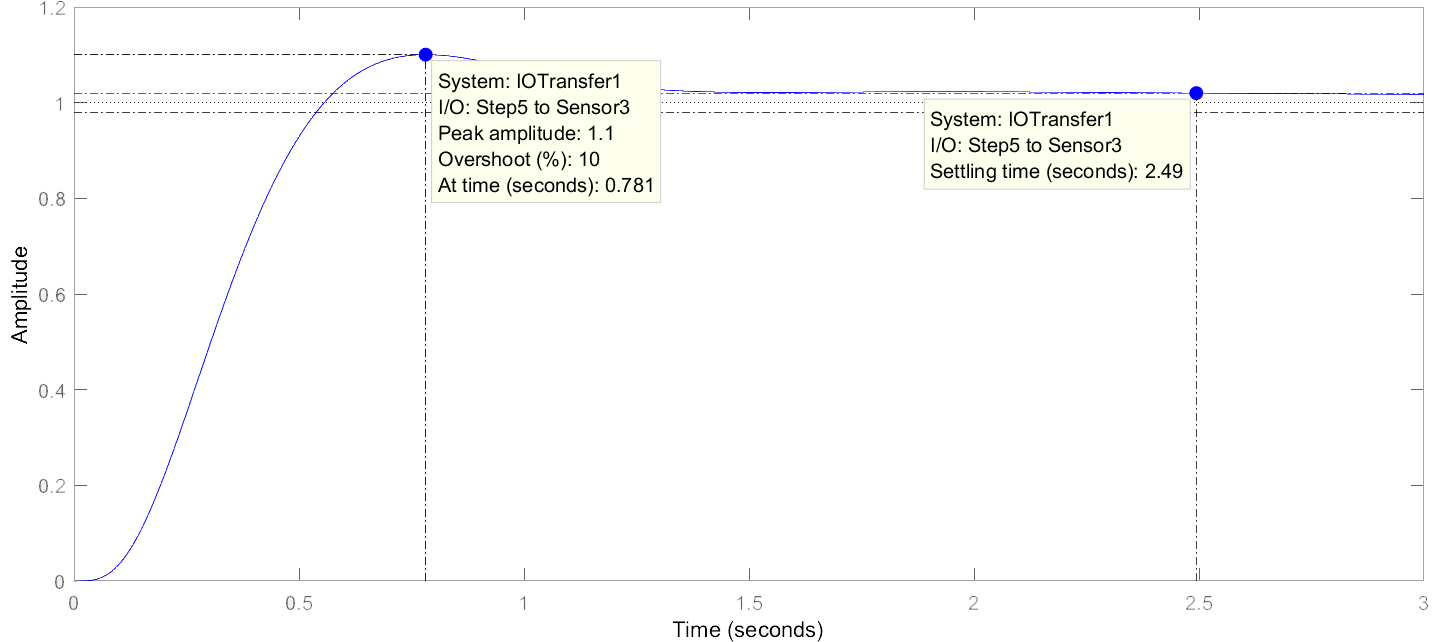
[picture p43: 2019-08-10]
Pictures/control design/step.PNG

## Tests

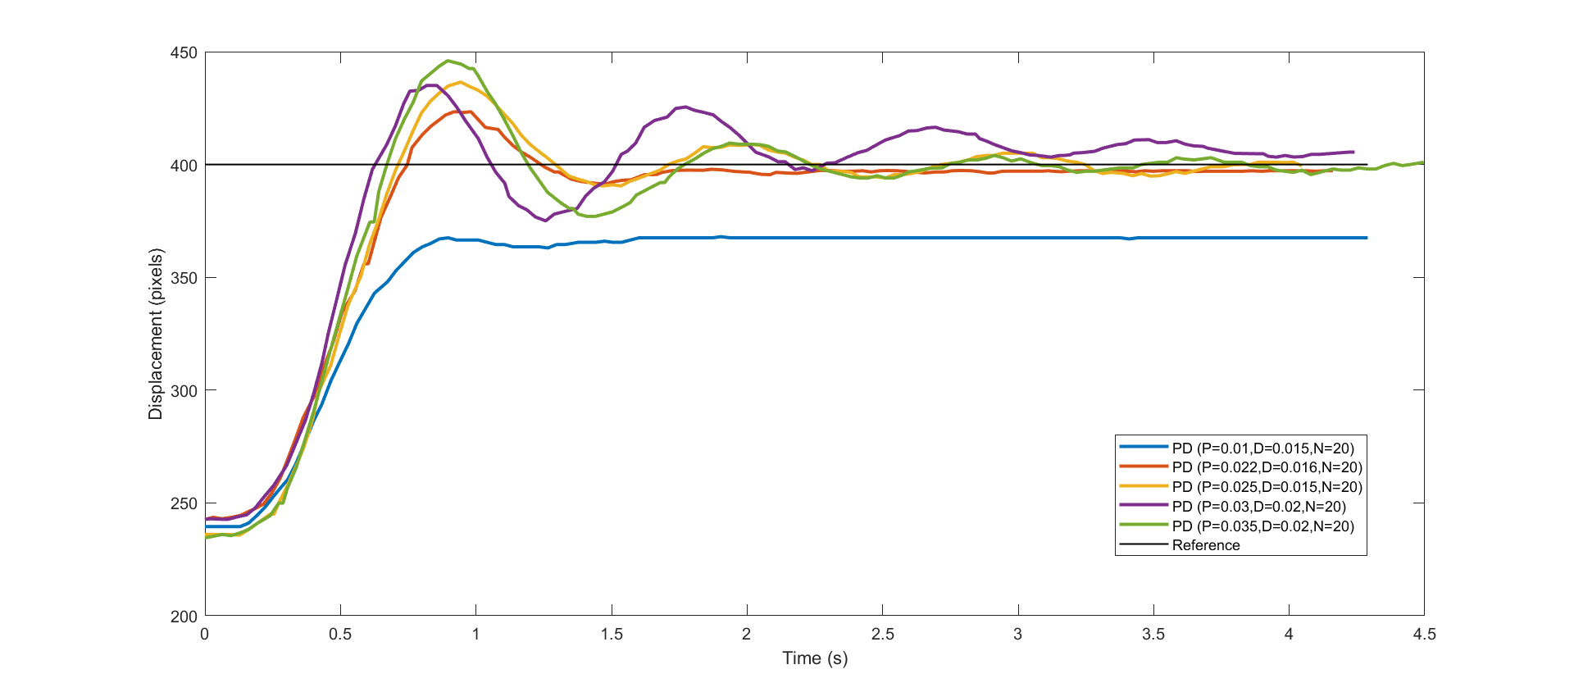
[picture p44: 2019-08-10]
Pictures/validation/PDControllers.png

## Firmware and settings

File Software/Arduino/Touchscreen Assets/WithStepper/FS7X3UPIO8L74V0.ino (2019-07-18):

/*
  Matthew M
  Ball on plat with 3 DOF
  Mega 2560

  microsteps: 32
  motor_steps_per_rev: 200
  -----------------------------------------------------------------
*/
#include "RunningMedian.h"
#include "RunningAverage.h"

RunningMedian samples_x = RunningMedian(10);
RunningMedian samples_y = RunningMedian(10);

RunningMedian samples_angle_x = RunningMedian(8); //10
RunningMedian samples_angle_y = RunningMedian(8); //10

RunningAverage average_a(15); //15
RunningAverage average_b(15); //15
RunningAverage average_c(15); //15

RunningAverage ACC_x(3);
RunningAverage ACC_y(3);

# define cycle_time 5 //run loop every ___ ms



bool compute = 0;
bool fast_compute = 0;
uint16_t  old_micros;
uint16_t  compute_time;

uint8_t loop_count;

//-----------------------------------------------------------
//interface knob---------------------------------------------
//---------------------------------------------------------
# define knob_a_pin 32
# define knob_b_pin 47
# define knob_btn_pin 45

uint8_t knob_a_last = 0;
uint8_t knob_a = 0;

uint8_t knob_b_last = 0;
uint8_t knob_b = 0;

uint8_t knob_btn = 1;
uint8_t knob_btn_last = 1;

uint8_t select_mode = 0;
float hold_count = 0;

uint8_t pattern = 0;
uint8_t pattern_rate = 20;
uint8_t pattern_rate_counter = 0;
uint16_t pattern_counter = 0;

bool loop_direction = 0;

int8_t sin_LUT[256] = {0,  3,  6,  9,  12, 16, 19, 22, 25, 28, 31, 34, 37, 40, 43, 46, 49, 51, 54, 57, 60, 63, 65, 68, 71, 73, 76, 78, 81, 83, 85, 88, 90, 92, 94, 96, 98, 100,  102,  104,  106,  107,  109,  111,  112,  113,  115,  116,  117,  118,  120,  121,  122,  122,  123,  124,  125,  125,  126,  126,  126,  127,  127,  127,  127,  127,  127,  127,  126,  126,  126,  125,  125,  124,  123,  122,  122,  121,  120,  118,  117,  116,  115,  113,  112,  111,  109,  107,  106,  104,  102,  100,  98, 96, 94, 92, 90, 88, 85, 83, 81, 78, 76, 73, 71, 68, 65, 63, 60, 57, 54, 51, 49, 46, 43, 40, 37, 34, 31, 28, 25, 22, 19, 16, 12, 9,  6,  3,  0,  -3, -6, -9, -12,  -16,  -19,  -22,  -25,  -28,  -31,  -34,  -37,  -40,  -43,  -46,  -49,  -51,  -54,  -57,  -60,  -63,  -65,  -68,  -71,  -73,  -76,  -78,  -81,  -83,  -85,  -88,  -90,  -92,  -94,  -96,  -98,  -100, -102, -104, -106, -107, -109, -111, -112, -113, -115, -116, -117, -118, -120, -121, -122, -122, -123, -124, -125, -125, -126, -126, -126, -127, -127, -127, -127, -127, -127, -127, -126, -126, -126, -125, -125, -124, -123, -122, -122, -121, -120, -118, -117, -116, -115, -113, -112, -111, -109, -107, -106, -104, -102, -100, -98,  -96,  -94,  -92,  -90,  -88,  -85,  -83,  -81,  -78,  -76,  -73,  -71,  -68,  -65,  -63,  -60,  -57,  -54,  -51,  -49,  -46,  -43,  -40,  -37,  -34,  -31,  -28,  -25,  -22,  -19,  -16,  -12,  -9, -6, -3};
int8_t cos_LUT[256] = {127, 127,  127,  127,  126,  126,  126,  125,  125,  124,  123,  122,  122,  121,  120,  118,  117,  116,  115,  113,  112,  111,  109,  107,  106,  104,  102,  100,  98, 96, 94, 92, 90, 88, 85, 83, 81, 78, 76, 73, 71, 68, 65, 63, 60, 57, 54, 51, 49, 46, 43, 40, 37, 34, 31, 28, 25, 22, 19, 16, 12, 9,  6,  3,  0,  -3, -6, -9, -12,  -16,  -19,  -22,  -25,  -28,  -31,  -34,  -37,  -40,  -43,  -46,  -49,  -51,  -54,  -57,  -60,  -63,  -65,  -68,  -71,  -73,  -76,  -78,  -81,  -83,  -85,  -88,  -90,  -92,  -94,  -96,  -98,  -100, -102, -104, -106, -107, -109, -111, -112, -113, -115, -116, -117, -118, -120, -121, -122, -122, -123, -124, -125, -125, -126, -126, -126, -127, -127, -127, -127, -127, -127, -127, -126, -126, -126, -125, -125, -124, -123, -122, -122, -121, -120, -118, -117, -116, -115, -113, -112, -111, -109, -107, -106, -104, -102, -100, -98,  -96,  -94,  -92,  -90,  -88,  -85,  -83,  -81,  -78,  -76,  -73,  -71,  -68,  -65,  -63,  -60,  -57,  -54,  -51,  -49,  -46,  -43,  -40,  -37,  -34,  -31,  -28,  -25,  -22,  -19,  -16,  -12,  -9, -6, -3, 0,  3,  6,  9,  12, 16, 19, 22, 25, 28, 31, 34, 37, 40, 43, 46, 49, 51, 54, 57, 60, 63, 65, 68, 71, 73, 76, 78, 81, 83, 85, 88, 90, 92, 94, 96, 98, 100,  102,  104,  106,  107,  109,  111,  112,  113,  115,  116,  117,  118,  120,  121,  122,  122,  123,  124,  125,  125,  126,  126,  126,  127,  127,  127};


//-----------------------------------------------------------------
//touch screen stuff
//-----------------------------------------------------------------
//     test screen at A,B,C,D,E
//
//      - - -T- - -       Y
//     |-|-|-|-|-|-|     /|
//     L- - -C- - -R      | -->X
//     |-|-|-|-|-|-|
//      - - -B- - -
// 
//enter values from measured_x_pos and measured_y_pos for initial screen calibration
//uncomment "Serial.print(measured_x_pos) Serial.println(measured_y_pos)" at bottom of main loop to display values


# define test_C_x 493
# define test_C_y 520

# define test_L_x 900
# define test_R_x 89

# define test_T_y 835
# define test_B_y 205

#define x_5v A0
#define x_gnd A1
#define y_5v  A2
#define y_gnd  A3

int16_t ball_x_pos;
int16_t ball_y_pos;
int16_t measured_x_pos;
int16_t corrected_x_pos;
int16_t measured_y_pos;
int16_t corrected_y_pos;

int8_t x_offset = 0;
int8_t y_offset = 0;

bool touch = 0;
int8_t detect_touch_filter = 0;
//----------------------------------------------------------------------
//PID stuff for ball position
//----------------------------------------------------------------------
int16_t set_x_pos = -300;
int16_t set_y_pos = 0;

int16_t x_pos_array [79];
int16_t y_pos_array [79];

float x_avg [16];
float y_avg [16];

int16_t FPGA_x_angle = 0;
int16_t FPGA_y_angle = 0;

float p_gain = 0.35;
float d_gain = 2.0;//550
float i_gain = 0.00;

float error_x = 0;
float error_y = 0;

float i_x = 0;
float i_y = 0;

float d_x = 0;
float d_y = 0;

float d_x_avg = 0;
float d_y_avg = 0;

float d_x_pos = 0;
float d_x_neg = 0;
float d_y_pos = 0;
float d_y_neg = 0;

int i;
int j;
//----------------------------------------------------------------------
//PID stuff for stepper motors
//----------------------------------------------------------------------
#include "PID_v1.h"

double set_angle_a, set_angle_b, set_angle_c;  //set values to PID
double measured_angle_a, measured_angle_b, measured_angle_c;  //actual measured values to send to PID
double set_speed_a, set_speed_b, set_speed_c;  //set speed from PID

double Kp = 0.03;  //proportional gain
double Ki = 0.0;
double Kd = 0.0;

#define max_speed 4  //max output value from PID
#define min_speed -4  //min output value from PID
#define PID_sample_time 10  //how often the PID algorithm evaluates in ms
#define deadband 3        // +/- number of counts to not respond 6

//PID myPID(&Input, &Output, &Setpoint, Kp, Ki, Kd, DIRECT);
PID PID_a(&measured_angle_a, &set_speed_a, &set_angle_a, Kp, Ki, Kd, DIRECT);
PID PID_b(&measured_angle_b, &set_speed_b, &set_angle_b, Kp, Ki, Kd, DIRECT);
PID PID_c(&measured_angle_c, &set_speed_c, &set_angle_c, Kp, Ki, Kd, DIRECT);

//xxxxxxxxxxxxxxxxxxxxxxxxxxxxxxxxxxxxxxxxxxxxxxxxxxxxxxxxxxxxxxxxxxxxxxxxxxxxx
//xxxxxxxxxxxxxxxxxxxxxxxxxxxxxxxxxxxxxxxxxxxxxxxxxxxxxxxxxxxxxxxxxxxxxxxxxxxxx
void setup()
{
  Serial.begin(230400);
  PID_setup();

  timer_setup();
  touch_screen_setup();


  set_angle_a = 0;
  set_angle_b = 0;
  set_angle_c = 0;
}
//xxxxxxxxxxxxxxxxxxxxxxxxxxxxxxxxxxxxxxxxxxxxxxxxxxxxxxxxxxxxxxxxxxxxxxxxxxxxx
//xxxxxxxxxxxxxxxxxxxxxxxxxxxxxxxxxxxxxxxxxxxxxxxxxxxxxxxxxxxxxxxxxxxxxxxxxxxxx
void loop()
{

  if (fast_compute == 1)
  {
    ball_patterns_and_display();
    fast_compute = 0;
  }



  if (compute == 1)
  {
    old_micros = micros();

    touch_screen();

    ball_PID();

    samples_angle_x.add(FPGA_x_angle);
    samples_angle_y.add(FPGA_y_angle);

    set_angle_a = 450.0 + samples_angle_y.getMedian();
    set_angle_b = 450.0 - float(samples_angle_y.getMedian()) * 0.52 + float(samples_angle_x.getMedian()) * 0.866;
    set_angle_c = 450.0 - float(samples_angle_y.getMedian()) * 0.52 - float(samples_angle_x.getMedian()) * 0.866;


    average_a.addValue(set_angle_a);
    set_angle_a = average_a.getAverage();
    average_b.addValue(set_angle_b);
    set_angle_b = average_b.getAverage();
    average_c.addValue(set_angle_c);
    set_angle_c = average_c.getAverage();

    //limit movement of motors
    if (set_angle_a < 5) set_angle_a = 5;
    else if (set_angle_a > 900) set_angle_a = 900;
    else set_angle_a = set_angle_a;

    if (set_angle_b < 5) set_angle_b = 5;
    else if (set_angle_b > 900) set_angle_b = 900;
    else set_angle_b = set_angle_b;

    if (set_angle_c < 5) set_angle_c = 5;
    else if (set_angle_c > 900) set_angle_c = 900;
    else set_angle_c = set_angle_c;

    calc_PID();






    //display values based on selected variable
    switch (select_mode)
    {
      case 1:
        Serial.print("kp ");
        Serial.println(p_gain);
        break;
      case 2:
        Serial.print("kd ");
        Serial.println(d_gain);
        break;
      case 3:
        Serial.print("ki ");
        Serial.println(i_gain);
        break;
      case 4:
        Serial.print(x_offset);
        Serial.println(" x offset");
        break;
      case 5:
        Serial.print(y_offset);
        Serial.println(" y offset");
        break;
      case 6:
        Serial.print(pattern);
        Serial.println(" pattern");
        break;
      case 7:
        Serial.print(pattern_rate);
        Serial.println(" pattern rate");
        break;
      case 8:
        Serial.print(loop_direction);
        Serial.println(" pattern direction");
        break;

      default:
        Serial.print(compute_time);
        Serial.println(" uS");
        break;
    }


    compute = 0;
    compute_time = micros() - old_micros;
  }
  else
  {
    //uncomment for screen calibration
    Serial.print(measured_x_pos);
    Serial.println(measured_y_pos);
  }
}
//xxxxxxxxxxxxxxxxxxxxxxxxxxxxxxxxxxxxxxxxxxxxxxxxxxxxxxxxxxxxxxxxxxxxxxxxxxxxx
//xxxxxxxxxxxxxxxxxxxxxxxxxxxxxxxxxxxxxxxxxxxxxxxxxxxxxxxxxxxxxxxxxxxxxxxxxxxxx

//----------------------------------------------------------------------
//quadrature control knob
//----------------------------------------------------------------------
void enc_knob_setup()
{
  pinMode (knob_a_pin, INPUT_PULLUP);
  pinMode (knob_b_pin, INPUT_PULLUP);
  pinMode (knob_btn_pin, INPUT_PULLUP);
}

float enc_knob(float count)
{
  knob_a = digitalRead(knob_a_pin);
  knob_b = digitalRead(knob_b_pin);
  knob_btn = digitalRead(knob_btn_pin);

  if ((knob_btn == LOW) && (knob_btn_last == HIGH))
  {
    if (select_mode < 8) select_mode = select_mode + 1;
    else select_mode = 0;
  }

  if ((knob_a_last == LOW) && (knob_a == HIGH))
  {
    if (knob_b == LOW)
    {
      count += 0.01;
    }
    else
    {
      count -= 0.01;
    }
  }
  else if ((knob_b_last == HIGH) && (knob_b == LOW))
  {
    if (knob_a == LOW)
    {
      count += 0.01;
    }
    else
    {
      count -= 0.01;
    }
  }

  knob_a_last = knob_a;
  knob_b_last = knob_b;
  knob_btn_last = knob_btn;
  return count;
}


//----------------------------------------------------------------------
//PID calculations for ball position
//----------------------------------------------------------------------
void ball_PID()
{
  error_x = (set_x_pos - corrected_x_pos) ;
  error_y = (set_y_pos - corrected_y_pos) ;

  //fill ball history array
  for (i = 0; i < 79; i ++)
  {
    x_pos_array [i + 1] = x_pos_array [i];
    y_pos_array [i + 1] = y_pos_array [i];
  }
  x_pos_array [0] = corrected_x_pos;
  y_pos_array [0] = corrected_y_pos;

  /*
    for (i = 0; i < 16; i ++)
    {
      x_avg[i] = float(x_pos_array [5 * i] + x_pos_array [5 * i + 1] + x_pos_array [5 * i + 2] + x_pos_array [5 * i + 3] + x_pos_array [5 * i + 4])/5.0;
      y_avg[i] = float(y_pos_array [5 * i] + y_pos_array [5 * i + 1] + y_pos_array [5 * i + 2] + y_pos_array [5 * i + 3] + y_pos_array [5 * i + 4])/5.0;
    }
  */


  for (i = 0; i < 16; i ++)
  {
    x_avg[i] = x_pos_array [i * 5]; //5
    y_avg[i] = y_pos_array [i * 5]; //5
  }

  d_x_pos = 322.0 * x_avg[0] + 217.0 * x_avg[1] + 110.0 * x_avg[2] + 35.0 * x_avg[3] + 25.0 * x_avg[13] + 98.0 * x_avg[14] + 203.0 * x_avg[15];
  d_y_pos = 322.0 * y_avg[0] + 217.0 * y_avg[1] + 110.0 * y_avg[2] + 35.0 * y_avg[3] + 25.0 * y_avg[13] + 98.0 * y_avg[14] + 203.0 * y_avg[15];

  d_x_neg = -42.0 * x_avg[4] - 87.0 * x_avg[5] - 134.0 * x_avg[6] - 149.0 * x_avg[7] - 166.0 * x_avg[8] - 151.0 * x_avg[9] - 138.0 * x_avg[10] - 93.0 * x_avg[11] - 50.0 * x_avg[12];
  d_y_neg = -42.0 * y_avg[4] - 87.0 * y_avg[5] - 134.0 * y_avg[6] - 149.0 * y_avg[7] - 166.0 * y_avg[8] - 151.0 * y_avg[9] - 138.0 * y_avg[10] - 93.0 * y_avg[11] - 50.0 * y_avg[12];

  d_x = (d_x_pos + d_x_neg) * d_gain / 28.56;
  d_y = (d_y_pos + d_y_neg) * d_gain / 28.56;

  //d_x = ((322.0 * x_avg[0] + 217.0 * x_avg[1] + 110.0 * x_avg[2] + 35.0 * x_avg[3] + 25.0 * x_avg[13] + 98.0 * x_avg[14] + 203.0 * x_avg[15] - 42.0 * x_avg[4] - 87.0 * x_avg[5] - 134.0 * x_avg[6] - 149.0 * x_avg[7] - 166.0 * x_avg[8] - 151.0 * x_avg[9] - 138.0 * x_avg[10] - 93.0 * x_avg[11] - 50.0 * x_avg[12]) * d_gain) / 2856.0;
  //d_y = ((322.0 * y_avg[0] + 217.0 * y_avg[1] + 110.0 * y_avg[2] + 35.0 * y_avg[3] + 25.0 * y_avg[13] + 98.0 * y_avg[14] + 203.0 * y_avg[15] - 42.0 * y_avg[4] - 87.0 * y_avg[5] - 134.0 * y_avg[6] - 149.0 * y_avg[7] - 166.0 * y_avg[8] - 151.0 * y_avg[9] - 138.0 * y_avg[10] - 93.0 * y_avg[11] - 50.0 * y_avg[12]) * d_gain) / 2856.0;



  //ACC_x.addValue(d_x);
  //ACC_y.addValue(d_y);

  d_x_avg = .5 * d_x + .5 * d_x_avg;
  d_y_avg = .5 * d_y + .5 * d_y_avg;


  if (error_x < 200 && error_x > -200) i_x += i_gain * error_x / 10.0;
  else i_x = 0;
  if (error_y < 200 && error_y > -200) i_y += i_gain * error_y / 10.0;
  else i_y = 0;


  if (i_gain == 0)
  {
    i_x = 0;
    i_y = 0;
  }

  if (i_x > 400.0) i_x = 400.0;
  else if (i_x < -400.0) i_x = -400.0;

  if (i_y > 400.0) i_y = 400.0;
  else if (i_y < -400.0) i_y = -400.0;

  FPGA_x_angle = error_x * p_gain + i_x - d_x_avg + x_offset;
  FPGA_y_angle = error_y * p_gain + i_y - d_y_avg + y_offset;


}

//----------------------------------------------------------------------
//PID calculations for stepper motors
//----------------------------------------------------------------------
void PID_setup()
{
  PID_a.SetMode(AUTOMATIC);
  PID_b.SetMode(AUTOMATIC);
  PID_c.SetMode(AUTOMATIC);

  PID_a.SetOutputLimits(min_speed, max_speed);
  PID_b.SetOutputLimits(min_speed, max_speed);
  PID_c.SetOutputLimits(min_speed, max_speed);

  PID_a.SetSampleTime(PID_sample_time);
  PID_b.SetSampleTime(PID_sample_time);
  PID_c.SetSampleTime(PID_sample_time);
}

void calc_PID()
{


  PID_a.Compute();
  PID_b.Compute();
  PID_c.Compute();

  //add deadbamd that the motors do nothing
  if ( measured_angle_a - set_angle_a < deadband && measured_angle_a - set_angle_a > -deadband) set_speed_a = 0;
  if ( measured_angle_b - set_angle_b < deadband && measured_angle_b - set_angle_b > -deadband) set_speed_b = 0;
  if ( measured_angle_c - set_angle_c < deadband && measured_angle_c - set_angle_c > -deadband) set_speed_c = 0;
}

//-------------------------------------------------------------------------
// touch screen measurements
//--------------------------------------------------------------------------
void touch_screen()
{
  detect_touch();  //is the screen being touched?

  //touch = 1;

  if (touch == 0)  //set position to (0,0) if not touched
  {
    ball_x_pos = test_C_x;
    ball_y_pos = test_C_y;
  }

  if (touch == 1) measure_touch();  //measure touch position if touched

  samples_x.add(ball_x_pos);
  samples_y.add(ball_y_pos);

  measured_x_pos = samples_x.getMedian();
  measured_y_pos = samples_y.getMedian();

  //normalize screen position to 0,0 at center and each inch is 100 count
  corrected_x_pos = measured_x_pos * 1200.0 / (test_R_x - test_L_x)  - test_C_x * 1200.0 / (test_R_x - test_L_x);
  corrected_y_pos = measured_y_pos * 800.0 / (test_T_y - test_B_y)   - test_C_y * 800.0 / (test_T_y - test_B_y);
}

void touch_screen_setup()
{
  //setup for "detect_touch()"
  pinMode(x_5v,  INPUT_PULLUP);
  pinMode(x_gnd,  INPUT_PULLUP);
  pinMode(y_5v,  INPUT);
  pinMode(y_gnd,  OUTPUT);

  digitalWrite(y_gnd, LOW);
}

void detect_touch()
{
  //debounce touch detection
  if (digitalRead(x_5v))
  {
    detect_touch_filter += 1;
    if (detect_touch_filter >= 3)
    {
      detect_touch_filter = 3;
      touch = 0;
    }
  }
  else
  {
    detect_touch_filter -= 1;
    if (detect_touch_filter <= -3)
    {
      detect_touch_filter = -3;
      touch = 1;
    }
  }
}

void measure_touch()
{
  //read x-position
  pinMode(x_5v,  OUTPUT);
  pinMode(x_gnd,  OUTPUT);
  pinMode(y_5v,  INPUT);
  pinMode(y_gnd,  INPUT);

  digitalWrite(x_5v, HIGH);
  digitalWrite(x_gnd, LOW);

  ball_x_pos = analogRead(y_5v);

  //read y-position
  pinMode(x_5v,  INPUT);
  pinMode(x_gnd,  INPUT);
  pinMode(y_5v,  OUTPUT);
  pinMode(y_gnd,  OUTPUT);

  digitalWrite(y_5v, HIGH);
  digitalWrite(y_gnd, LOW);

  ball_y_pos = analogRead(x_5v);

  //setup for "detect_touch()"
  pinMode(x_5v,  INPUT_PULLUP);
  pinMode(x_gnd,  INPUT_PULLUP);
  pinMode(y_5v,  INPUT);
  pinMode(y_gnd,  OUTPUT);

  digitalWrite(y_gnd, LOW);
}

//-----------------------------------------------------------------------
//loop timing stuff
//------------------------------------------------------------------------
void timer_setup()
{
  // Timer0 is already used for "millis()", just interrupt somewhere
  // in the middle to toggle the "compute" values
  OCR0A = 0xAF;
  TIMSK0 |= _BV(OCIE0A);
}

//timer interrupt from timer0 every ~1ms
SIGNAL(TIMER0_COMPA_vect)
{
  fast_compute = 1;
  if (loop_count < cycle_time) loop_count++;
  else
  {
    compute = 1;
    loop_count = 0;
  }
}

//------------------------------------------------------------------------
//stuff to control the stepper motors
//------------------------------------------------------------------------
void stepper_setup()
{




  cli();//stop interrupts



  sei(); // Start Interrupt

}

void stepper_run( uint8_t motorNumber, float motor_speed)
{
  bool dir;  //motor direction
  uint16_t PWM_count;

  //determine needed motor direction and make speed pos.
  if (motor_speed < 0)
  {
    dir = 0;
    motor_speed = abs(motor_speed);
  }
  else dir = 1;

  if (motor_speed > 0)
  {
    PWM_count = 5000 / motor_speed;  //calculate needed compare value for speed
  }
  else PWM_count = 0;  //set compare value to 0 to keep stepper output from toggling when zero velocity needed



}

void motor_power(bool power)
{
  if (power == 1)
  {

  }
  else
  {

  }
}

//-------------------------------------------------------------------------------
//ball patterns!!!
//------------------------------------------------------------------------------

void ball_patterns_and_display()
{
  if (pattern_rate_counter < pattern_rate) pattern_rate_counter ++;
  else
  {
    
    if (loop_direction == 1) pattern_counter ++;
    else pattern_counter --;
    pattern_rate_counter = 0;
  }

  //calculate parametric ball patterns
  switch (pattern)
  {
    case 1:
      if (uint8_t(pattern_counter) < 64) 
      {
        set_x_pos = 300;
        set_y_pos = 300;
      }
      else if (uint8_t(pattern_counter) < 128) 
      {
        set_x_pos = 300;
        set_y_pos = -300;
      }
      else if (uint8_t(pattern_counter) < 192) 
      {
        set_x_pos = -300;
        set_y_pos = -300;
      }
      else 
      {
        set_x_pos = -300;
        set_y_pos = 300;
      }
      break;

    case 2:
      set_x_pos = cos_LUT[uint8_t(pattern_counter)];
      set_y_pos = sin_LUT[uint8_t(pattern_counter)];
      break;
    case 3:
      set_x_pos = 2 * cos_LUT[uint8_t(pattern_counter)];
      set_y_pos = 2 * sin_LUT[uint8_t(pattern_counter)];
      break;
    case 4:
      set_x_pos = 3 * cos_LUT[uint8_t(pattern_counter)];
      set_y_pos = 3 * sin_LUT[uint8_t(pattern_counter)];
      break;
    case 5:
      set_x_pos = 3 * sin_LUT[uint8_t(pattern_counter/2 +64)];
      set_y_pos = 3 * sin_LUT[uint8_t(pattern_counter)];
      break;
    case 6:
      set_x_pos = 3 * sin_LUT[uint8_t(pattern_counter/2+64)];
      set_y_pos = 3 * sin_LUT[uint8_t(pattern_counter/3 )];
      break;
    case 7:
      set_x_pos = 3 * sin_LUT[uint8_t(pattern_counter/4+64)];
      set_y_pos = 3 * sin_LUT[uint8_t(pattern_counter/3 )];
      break;
    case 8:
      set_x_pos = 3 * sin_LUT[uint8_t(pattern_counter/4+64)];
      set_y_pos = 3 * sin_LUT[uint8_t(pattern_counter/5 )];
      break;

    default:
      set_x_pos = 0;
      set_y_pos = 0;
      break;
  }

  //adjust variables with quadrature control knob 
  switch (select_mode)
  {
    case 1:
      p_gain = enc_knob(p_gain);
      break;
    case 2:
      d_gain = enc_knob(d_gain);
      break;
    case 3:
      i_gain = enc_knob(i_gain);
      break;
    case 4:
      x_offset = x_offset - 100 * x_offset + 100 * enc_knob(x_offset);
      break;
    case 5:
      y_offset = y_offset - 100 * y_offset + 100 * enc_knob(y_offset);
      break;
    case 6:
      pattern = pattern - 100 * pattern + 100 * enc_knob(pattern);
      if (pattern > 8) pattern = 0;
      break;
    case 7:
      pattern_rate = pattern_rate - 100 * pattern_rate + 100 * enc_knob(pattern_rate);
      break;
    case 8:
      loop_direction = loop_direction - 100 * loop_direction + 100 * enc_knob(loop_direction);
      break;

    default:
      hold_count = enc_knob(hold_count);
      break;
  }
}

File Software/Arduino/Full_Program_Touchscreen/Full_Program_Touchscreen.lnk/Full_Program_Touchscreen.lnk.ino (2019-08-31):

/*=================================
This code demostrates 4-Wire Touch screen 
interfacing with Arduino

blog.circuits4you.com
www.circuits4you.com

4- Wire Touchscreen Connections
A0=====X+
A1=====X-
A2=====Y+
A3=====Y-

Make sure you put pull-down resistors (10Kohms) on A0 and A2
=================================*/
//Define your Touch screen connections
#define X1 A0
#define X2 A1
#define Y1 A2
#define Y2 A3
//Define your screen resolution as per your Touch screen (Max: 1024)
#define Xresolution 234 //128
#define Yresolution 175 //64

#include <Servo.h>
#include <time.h>

Servo servoA;
Servo servoB;

int readX()
{
   float X = 0;
   pinMode(Y1,INPUT);
   pinMode(Y2,INPUT);  
   digitalWrite(Y2,LOW);
   pinMode(X1,OUTPUT);
   digitalWrite(X1,HIGH);
   pinMode(X2,OUTPUT);
   digitalWrite(X2,LOW);
   delay(5);
   X += analogRead(Y1);
   if (X != 0)
   {
    X = map(X, 50, 860 , - Xresolution / 2, Xresolution / 2); //Reads X axis touch position
   }
   return X;
}


int readY()
{
   int Y = 0;
   pinMode(X1,INPUT);
   pinMode(X2,INPUT);
   digitalWrite(X2,LOW);
   pinMode(Y1,OUTPUT);
   digitalWrite(Y1,HIGH);
   pinMode(Y2,OUTPUT);
   digitalWrite(Y2,LOW);
   delay(5);
   Y = analogRead(X1);
   if (Y != 0){
    Y = map(Y,100, 820 , - Yresolution / 2, Yresolution / 2); 
   }
   return Y;
}


void setup()
{
   Serial.begin(19200);
  
   servoA.attach(10, 500, 2600);      //servo A
   servoB.attach(6, 500, 2600);    //servo B
   

}

float X = 0, Y= 0;
float prevX = 0 , prevY = 0;
float Kp = 0.035, Ki = 0.000, Kd = 0.015;
float totalErrorX = 0, totalErrorY = 0;
float prevErrorX = 0, prevErrorY=0;
float prevDerivX = 0, prevDerivY = 0;
float Cdx=0, Cdy=0;
int refX = 0, refY = 0;
float Ix = 0, Iy = 0;
float errorX = 0, errorY = 0;
float dc = 6.2 ,dm = 1.7 ;
float K = dc / dm;
float angleA = 90;
float angleB = 90;
float windupX = 0;
float windupY = 0;
float Ts = 0;
float Time = 0;
int N = 20;

void loop()
{
  Time = millis();
  //Display X and Y on Serial Monitor
   prevX = X;
   prevY = Y;
   prevDerivX = Cdx;
   prevDerivY = Cdy;
   prevErrorX = errorX;
   prevErrorY = errorY;

   X = readX();
   Y = readY();
   //X = 0.9048*prevX + 0.09516*X;
   //Y = 0.9048*prevY + 0.09516*Y;
   
//   for (cnt = 0; cnt < 5; cnt++){
//       X += readX();
//       Y += readY();
//       delay(2);
//   }

//   X = X/cnt;
//   Y = Y/cnt;
   
   errorX = refX - X;
   errorY = refY - Y;
   
   //windupX = Ki * (totalErrorX); // anti windupX
   
   //windupY = Ki * (totalErrorY); // anti windupY

   Cdx =  (Kd*N*(errorX-prevErrorX)+prevDerivX)/(1+N*Ts);
   Cdy =  (Kd*N*(errorY-prevErrorY)+prevDerivY)/(1+N*Ts);
   
   Ix = Kp * (errorX) + windupX + Cdx;
   Iy = Kp * (errorY) + windupY + Kd *(prevY - Y)/Ts;
   angleA = (K * Ix)+90;
   angleB = -(K * Iy)+90;


   if (angleA > 180) angleA = 180;
   if (angleA < 0) angleA = 0;
   if (angleB > 180) angleB = 180;
   if (angleB < 0) angleB = 0;
   servoA.write( angleA);
   servoB.write(angleB);

   totalErrorX += errorX;
   totalErrorY += errorY;
   
   Serial.print("X = ");  
   Serial.print(X);
   Serial.print(" ,Y = ");
   Serial.print(Y);
   Serial.print(" ,Ts = ");  
   Serial.println(Ts);
   //Serial.print(" ,errorX = ");  
   //Serial.print(errorX);
   //Serial.print(" ,errorY = ");
   //Serial.print(errorY);
   //Serial.print(" ,angleA = ");
   //Serial.print(angleA);
   //Serial.print(" ,angleB = ");
   //Serial.println(angleB);
   Ts = (millis() - Time)/1000;
}

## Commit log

2019-03-19 Initialize Repo
    [ArduinoMega.SLDPRT, ArduinoMega_STEP_AP203.STEP, Assem.SLDASM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]
2019-03-20 Add Arduino Servo Calibration file
2019-03-24 Modify 3D Files
    [01.SLDPRT, 02.x_t, 03.STEP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]
2019-03-31 Modify 3D Parts for printing
    [Assem1.SLDASM, Base.SLDPRT, Base.STL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]
2019-05-09 Modify 3d Parts: camera slider, Plugs, Servo Arm
    [Camera_Slider.STL, Camera_Slider.sldprt, Copy of Part10.sldprt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]
2019-06-24 fix parts for 3d printing
    [Copy of Part10.sldprt, Plug.STL]
2019-07-03 Added Arduino Tests
2019-07-10 Modify CAD Assembly
    [Assem1.SLDASM, Base.SLDPRT, Camera_Slider.STL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]
2019-07-18 Cad modifications
    [Assem1.SLDASM, Assembly Board.DXF, Ball Board.DXF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]
2019-08-10 Modifying Dimensions and Drawings
    [ASSY_BERG_UJ3_U-JOINT_0250 SHAFT.sldasm, Assem1.SLDASM, Base.SLDPRT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]
2019-08-11 Modify Repository
    [Ball.SLDPRT, Ball3 end.SLDPRT, Ball3 start.SLDPRT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]
2019-08-12 ignore big CAD files
    [ArduinoMega.SLDPRT, ArduinoMega_STEP_AP203.STEP]
